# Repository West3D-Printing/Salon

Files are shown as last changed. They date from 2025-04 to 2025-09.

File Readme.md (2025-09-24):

Files and documentation for the Salon board for Casa
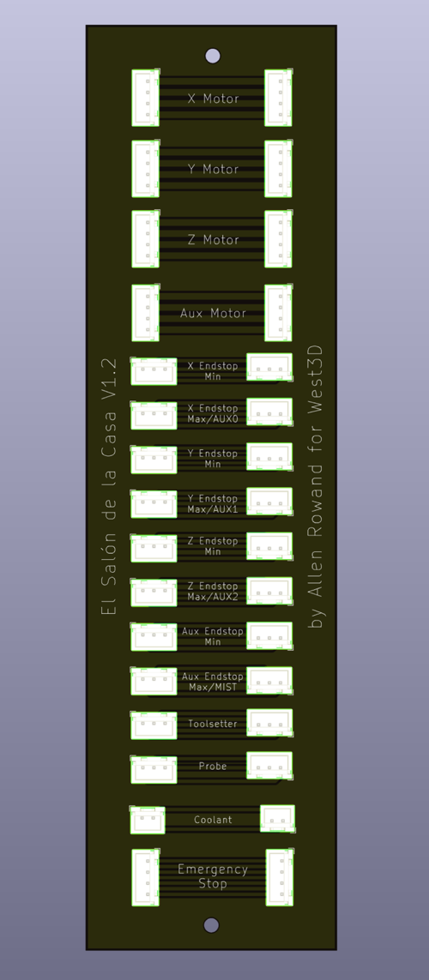
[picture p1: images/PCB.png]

# Why?
We wanted to provide a simple and inexpensive way to connect your Milo to the electronics bay of your Casa while allowing you to easily remove the Milo for service. The Salon PCB provides a "patchbay" to interconnect your MCU and the mill.

# How?
You can purchase the Salon board with wiring bundles at West3D here: https://west3d.com/products/milo-salon-de-la-casa-breakout-board-and-wiring-kit-for-milo-casa You're also welcome to produce your own PCB with our [KiCad files](kicad). The wiring is a simple 1:1 between the electronics bay and mill.

[STLs](stls) for a 3D printed PCB mount are in this repo. **There is now an updated version of the back mount with some improvements:**
1) More enclosed to keep chaff away from the connectors
2) An opening on the back to run wires upward for lighting (or whatever)
3) Slots at the bottom for zip ties to provide strain relief on the cables

The front hasn't changed and works with either back.

We've also included printable thumbscrews. These use a Voron standard brass heat insert and an M3x10 BHCS or SHCS, and make it easy to remove the Salon front without needing tools.
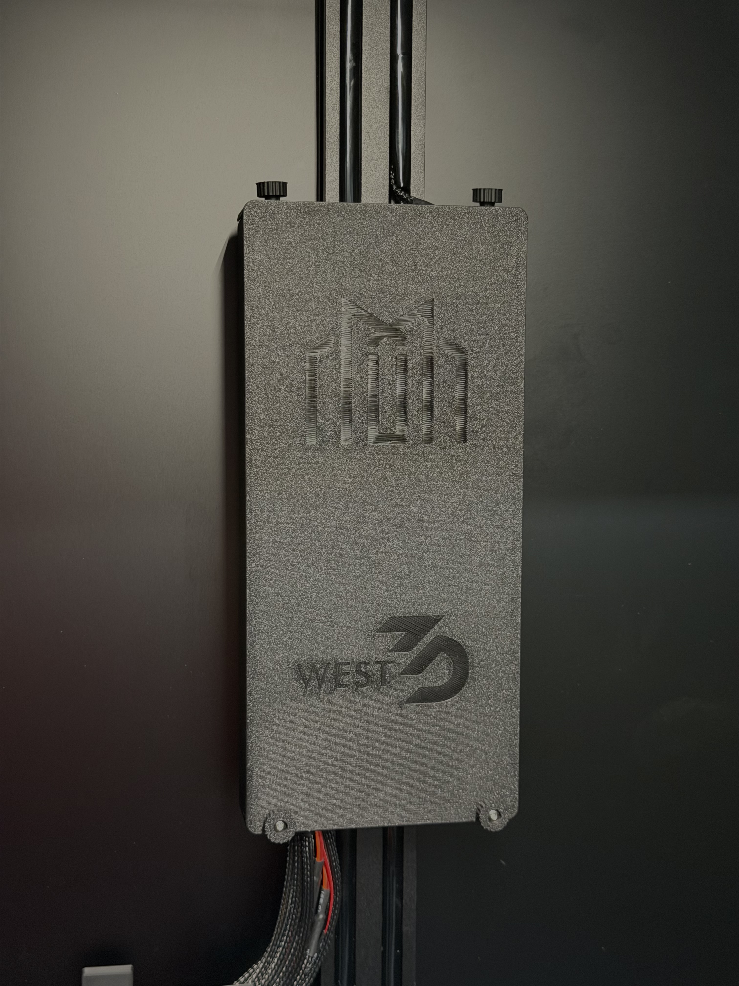
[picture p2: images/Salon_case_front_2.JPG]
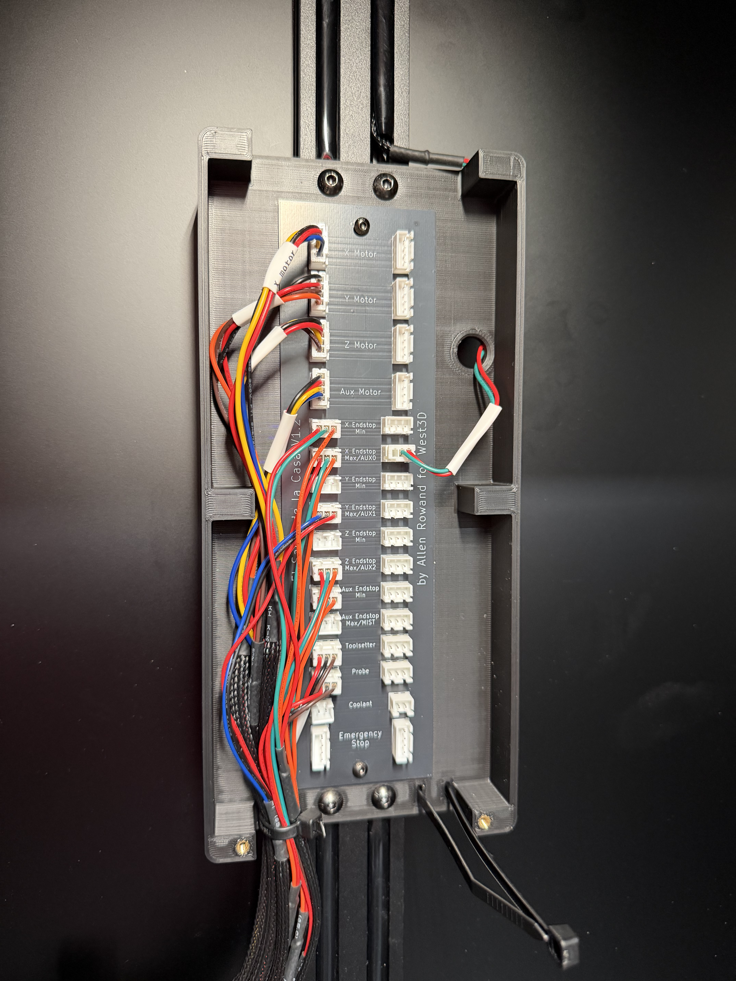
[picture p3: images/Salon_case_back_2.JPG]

# Setup
Hardware you'll need for the mount:
| Fastener  | Quantity |
| --- | --- |
| M3x6 screw  | 2  |
| M3x8 screw  | 4  |
| M5x8 screw  | 4  |
| M3 heatset  | 6  |
| M5 roll-in nut  | 4  |

- Print the PCB mount.
- Insert two "Voron standard" M3 heat inserts in the back of the mount to hold the PCB, as well as two in the top and another two in the lower legs to hold the front of the case.
- The PCB is held in place with two M3x6 screws.
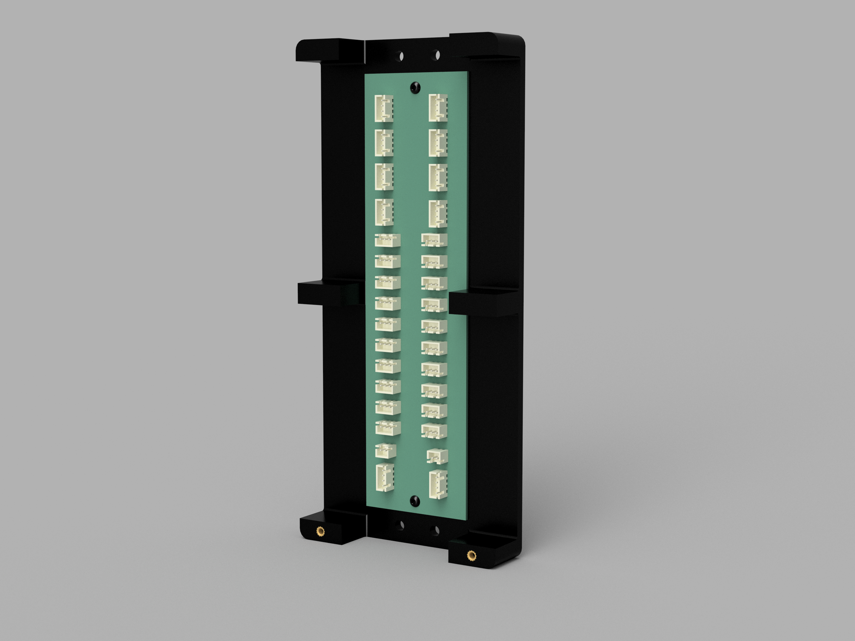
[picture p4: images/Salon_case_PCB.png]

<sub>Please note this is the V1 mount back in the render</sub>
- After installing the PCB, attach the back of the mount to the rear upright in the Casa with four M5x8 screws and roll-in nuts.
- Connect the wiring from the electronics bay to the PCB, then connect the wiring from the mill. There's no defined in or out sides, all connections are are parallel.
- Once everything is patched install the front cover with four M3x8 screws to help keep chips away from the connections.

# What about all these other connections, like Aux?
We wanted to bring all the available ports of the Scylla board into the work area for whatever additional hardware you want to control. Caselights, air, coolant, disco balls…

# Why "Salon"?
The Casa is the "house" for the Milo- the central room in a casa is often called the salon.
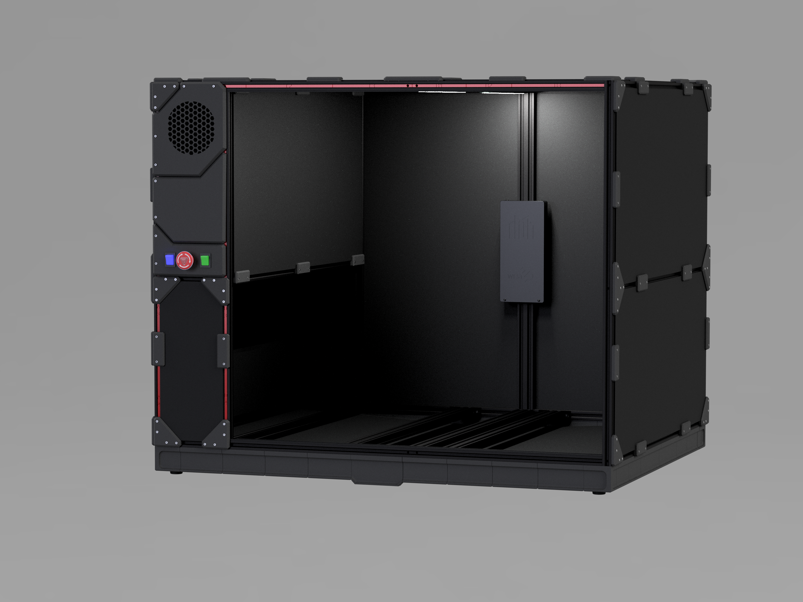
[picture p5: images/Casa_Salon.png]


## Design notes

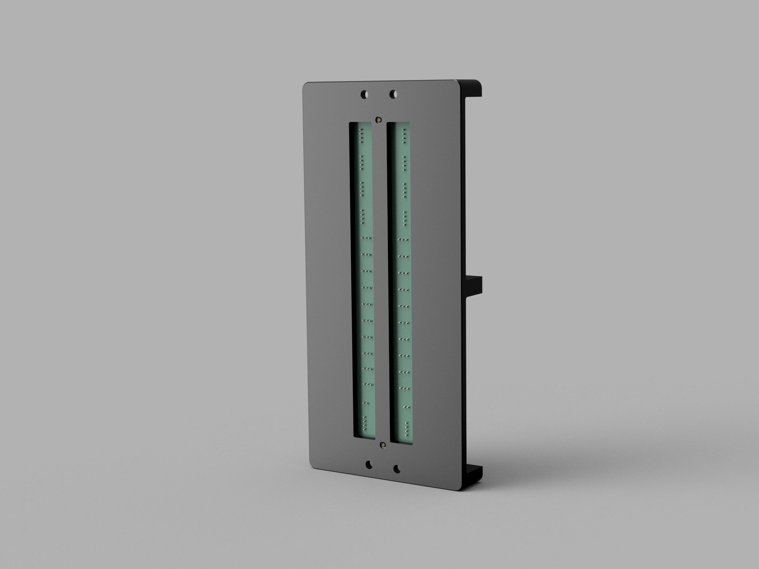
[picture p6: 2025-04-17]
images/Salon_case_back.png

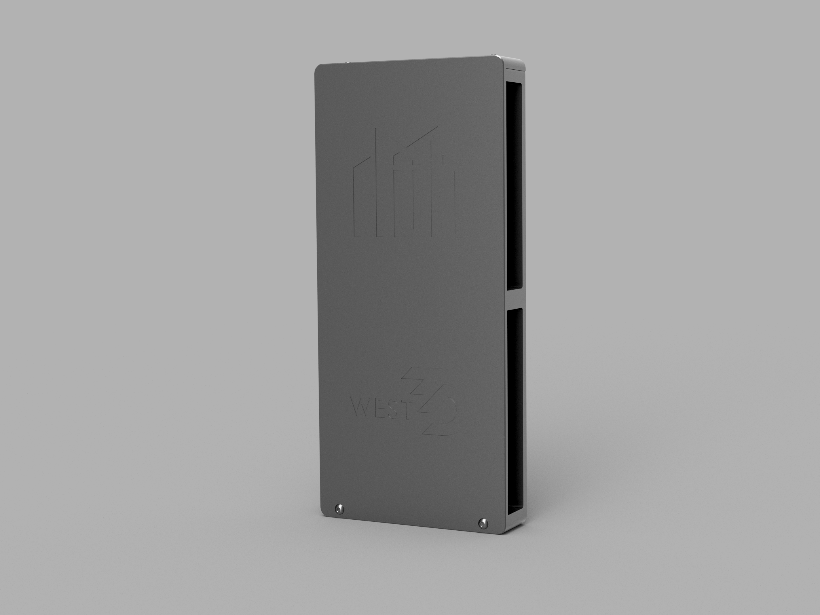
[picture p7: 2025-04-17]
images/Salon_case_front.png

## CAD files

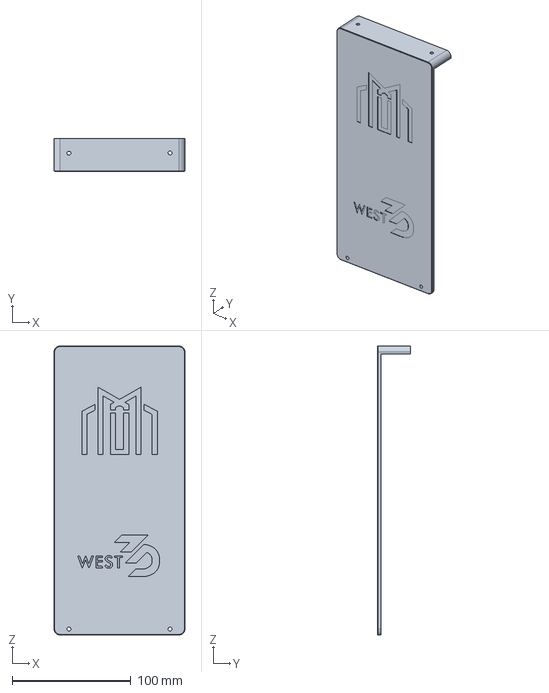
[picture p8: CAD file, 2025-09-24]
CAD/Salon case front.step
110.0 x 28.0 x 243.0 mm

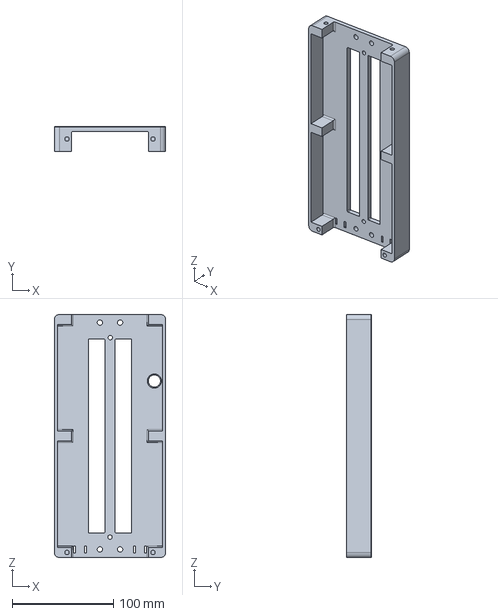
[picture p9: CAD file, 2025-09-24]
CAD/Salon case back V2.step
110.0 x 25.0 x 240.0 mm

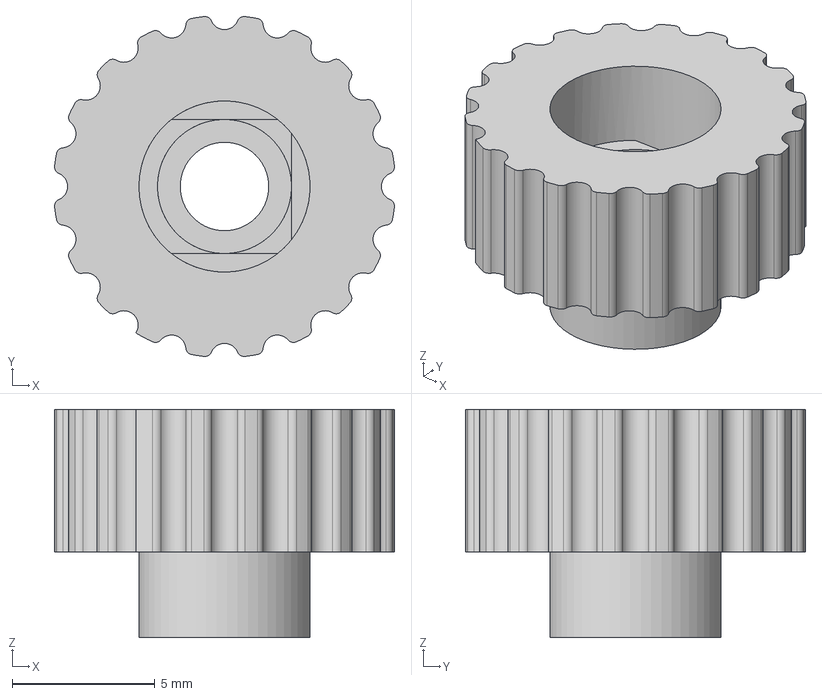
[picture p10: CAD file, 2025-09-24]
CAD/Thumbscrew.step
11.9 x 11.9 x 8.00 mm

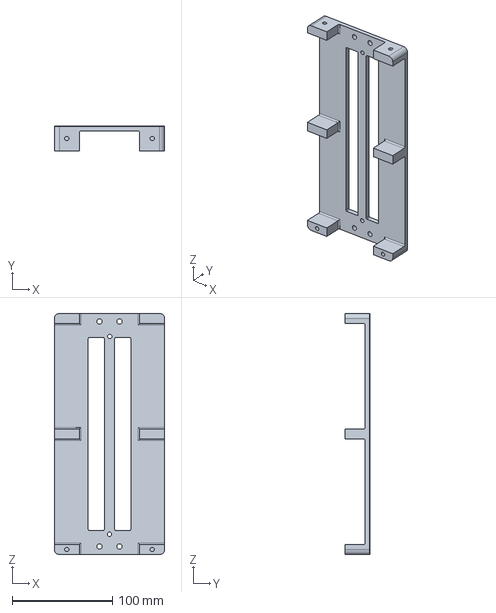
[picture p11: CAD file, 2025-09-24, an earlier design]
CAD/Salon case back V1.step
110.0 x 25.0 x 240.0 mm

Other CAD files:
stls/Salon_case_BACK_V1.stl
stls/Salon_case_BACK_V2.stl
stls/Salon_case_FRONT.stl
stls/Thumbscrew.stl

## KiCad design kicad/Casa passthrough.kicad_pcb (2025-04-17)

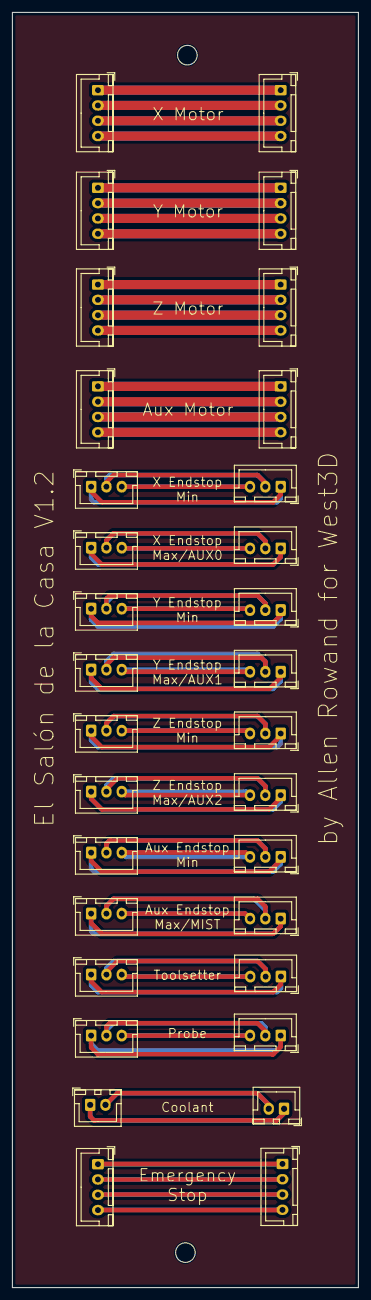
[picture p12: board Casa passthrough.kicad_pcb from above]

Board: 2 copper layers, 56.5 x 208.3 mm, 32 parts (0 on the bottom side), 52 nets.

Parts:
Aux_Endstop_Max_IN1: Conn_01x03; JST_XH_B3B-XH-A_1x03_P2.50mm_Vertical
Aux_Endstop_Max_OUT1: Conn_01x03; JST_XH_B3B-XH-A_1x03_P2.50mm_Vertical
Aux_Endstop_Min_IN1: Conn_01x03; JST_XH_B3B-XH-A_1x03_P2.50mm_Vertical
Aux_Endstop_Min_OUT1: Conn_01x03; JST_XH_B3B-XH-A_1x03_P2.50mm_Vertical
Aux_Motor_IN1: Conn_01x04; JST_XH_B4B-XH-A_1x04_P2.50mm_Vertical
Aux_Motor_OUT1: Conn_01x04; JST_XH_B4B-XH-A_1x04_P2.50mm_Vertical
Coolant_IN1: Conn_01x03; JST_XH_B2B-XH-A_1x02_P2.50mm_Vertical
Coolant_OUT1: Conn_01x03; JST_XH_B2B-XH-A_1x02_P2.50mm_Vertical
EStop_OUT1: Conn_01x04; JST_XH_B4B-XH-A_1x04_P2.50mm_Vertical
Estop_IN1: Conn_01x04; JST_XH_B4B-XH-A_1x04_P2.50mm_Vertical
Probe_IN1: Conn_01x03; JST_XH_B3B-XH-A_1x03_P2.50mm_Vertical
Probe_OUT1: Conn_01x03; JST_XH_B3B-XH-A_1x03_P2.50mm_Vertical
Toolsetter_IN1: Conn_01x03; JST_XH_B3B-XH-A_1x03_P2.50mm_Vertical
Toolsetter_OUT1: Conn_01x03; JST_XH_B3B-XH-A_1x03_P2.50mm_Vertical
X_Endstop_Max_IN1: Conn_01x03; JST_XH_B3B-XH-A_1x03_P2.50mm_Vertical
X_Endstop_Max_OUT1: Conn_01x03; JST_XH_B3B-XH-A_1x03_P2.50mm_Vertical
X_Endstop_Min_IN1: Conn_01x03; JST_XH_B3B-XH-A_1x03_P2.50mm_Vertical
X_Endstop_Min_OUT1: Conn_01x03; JST_XH_B3B-XH-A_1x03_P2.50mm_Vertical
X_Motor_IN1: Conn_01x04; JST_XH_B4B-XH-A_1x04_P2.50mm_Vertical
X_Motor_OUT1: Conn_01x04; JST_XH_B4B-XH-A_1x04_P2.50mm_Vertical
Y_Endstop_Max_IN1: Conn_01x03; JST_XH_B3B-XH-A_1x03_P2.50mm_Vertical
Y_Endstop_Max_OUT1: Conn_01x03; JST_XH_B3B-XH-A_1x03_P2.50mm_Vertical
Y_Endstop_Min_IN1: Conn_01x03; JST_XH_B3B-XH-A_1x03_P2.50mm_Vertical
Y_Endstop_Min_OUT1: Conn_01x03; JST_XH_B3B-XH-A_1x03_P2.50mm_Vertical
Y_Motor_IN1: Conn_01x04; JST_XH_B4B-XH-A_1x04_P2.50mm_Vertical
Y_Motor_OUT1: Conn_01x04; JST_XH_B4B-XH-A_1x04_P2.50mm_Vertical
Z_Endstop_Max_IN1: Conn_01x03; JST_XH_B3B-XH-A_1x03_P2.50mm_Vertical
Z_Endstop_Max_OUT1: Conn_01x03; JST_XH_B3B-XH-A_1x03_P2.50mm_Vertical
Z_Endstop_Min_IN1: Conn_01x03; JST_XH_B3B-XH-A_1x03_P2.50mm_Vertical
Z_Endstop_Min_OUT1: Conn_01x03; JST_XH_B3B-XH-A_1x03_P2.50mm_Vertical
Z_Motor_IN1: Conn_01x04; JST_XH_B4B-XH-A_1x04_P2.50mm_Vertical
Z_Motor_OUT1: Conn_01x04; JST_XH_B4B-XH-A_1x04_P2.50mm_Vertical

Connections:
unnamed: Aux_Endstop_Max_IN1.1, Aux_Endstop_Max_OUT1.1
unnamed: Aux_Endstop_Max_IN1.2, Aux_Endstop_Max_OUT1.2
unnamed: Aux_Endstop_Max_IN1.3, Aux_Endstop_Max_OUT1.3
unnamed: Aux_Endstop_Min_IN1.1, Aux_Endstop_Min_OUT1.1
unnamed: Aux_Endstop_Min_IN1.2, Aux_Endstop_Min_OUT1.2
unnamed: Aux_Endstop_Min_IN1.3, Aux_Endstop_Min_OUT1.3
unnamed: Aux_Motor_IN1.1, Aux_Motor_OUT1.1
unnamed: Aux_Motor_IN1.2, Aux_Motor_OUT1.2
unnamed: Aux_Motor_IN1.3, Aux_Motor_OUT1.3
unnamed: Aux_Motor_IN1.4, Aux_Motor_OUT1.4
unnamed: Coolant_IN1.1, Coolant_OUT1.1
unnamed: Coolant_IN1.2, Coolant_OUT1.2
unnamed: EStop_OUT1.1, Estop_IN1.1
unnamed: EStop_OUT1.2, Estop_IN1.2
unnamed: EStop_OUT1.3, Estop_IN1.3
unnamed: EStop_OUT1.4, Estop_IN1.4
unnamed: Probe_IN1.1, Probe_OUT1.1
unnamed: Probe_IN1.2, Probe_OUT1.2
unnamed: Probe_IN1.3, Probe_OUT1.3
unnamed: Toolsetter_IN1.1, Toolsetter_OUT1.1
unnamed: Toolsetter_IN1.2, Toolsetter_OUT1.2
unnamed: Toolsetter_IN1.3, Toolsetter_OUT1.3
unnamed: X_Endstop_Max_IN1.1, X_Endstop_Max_OUT1.1
unnamed: X_Endstop_Max_IN1.2, X_Endstop_Max_OUT1.2
unnamed: X_Endstop_Max_IN1.3, X_Endstop_Max_OUT1.3
unnamed: X_Endstop_Min_IN1.1, X_Endstop_Min_OUT1.1
unnamed: X_Endstop_Min_IN1.2, X_Endstop_Min_OUT1.2
unnamed: X_Endstop_Min_IN1.3, X_Endstop_Min_OUT1.3
unnamed: X_Motor_IN1.1, X_Motor_OUT1.1
unnamed: X_Motor_IN1.2, X_Motor_OUT1.2
unnamed: X_Motor_IN1.3, X_Motor_OUT1.3
unnamed: X_Motor_IN1.4, X_Motor_OUT1.4
unnamed: Y_Endstop_Max_IN1.1, Y_Endstop_Max_OUT1.1
unnamed: Y_Endstop_Max_IN1.2, Y_Endstop_Max_OUT1.2
unnamed: Y_Endstop_Max_IN1.3, Y_Endstop_Max_OUT1.3
unnamed: Y_Endstop_Min_IN1.1, Y_Endstop_Min_OUT1.1
unnamed: Y_Endstop_Min_IN1.2, Y_Endstop_Min_OUT1.2
unnamed: Y_Endstop_Min_IN1.3, Y_Endstop_Min_OUT1.3
unnamed: Y_Motor_IN1.1, Y_Motor_OUT1.1
unnamed: Y_Motor_IN1.2, Y_Motor_OUT1.2
unnamed: Y_Motor_IN1.3, Y_Motor_OUT1.3
unnamed: Y_Motor_IN1.4, Y_Motor_OUT1.4
unnamed: Z_Endstop_Max_IN1.1, Z_Endstop_Max_OUT1.1
unnamed: Z_Endstop_Max_IN1.2, Z_Endstop_Max_OUT1.2
unnamed: Z_Endstop_Max_IN1.3, Z_Endstop_Max_OUT1.3
unnamed: Z_Endstop_Min_IN1.1, Z_Endstop_Min_OUT1.1
unnamed: Z_Endstop_Min_IN1.2, Z_Endstop_Min_OUT1.2
unnamed: Z_Endstop_Min_IN1.3, Z_Endstop_Min_OUT1.3
unnamed: Z_Motor_IN1.1, Z_Motor_OUT1.1
unnamed: Z_Motor_IN1.2, Z_Motor_OUT1.2
unnamed: Z_Motor_IN1.3, Z_Motor_OUT1.3
unnamed: Z_Motor_IN1.4, Z_Motor_OUT1.4

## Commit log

2025-04-17 Initial upload
    [Casa passthrough-B_Cu.gbr, Casa passthrough-B_Mask.gbr, Casa passthrough-B_Paste.gbr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]
2025-04-21 Upload case STLs
    [Salon_case_BACK.stl, Salon_case_FRONT.stl]
2025-09-24 Add V2 and thumbscrew STLs
    [Salon_case_BACK_V1.stl, Salon_case_BACK_V2.stl, Thumbscrew.step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]
2025-09-24 Upload step files
    [Salon case back V1.step, Salon case back V2.step, Salon case front.step]
